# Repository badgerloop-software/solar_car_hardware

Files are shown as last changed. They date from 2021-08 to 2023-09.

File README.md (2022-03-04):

# solar_car_hardware
Repository for solar car electrical hardware made in Altium Designer. This project is set up to provide all documentation, design and data validation required for the Badgerloop Solar Car PCBs. This repository builds off of our previous work in the SpaceX Hyperloop Competition.

## Prerequisites
Altium only works on Windows. See  [Altium System Requirements](https://www.altium.com/documentation/18.0/display/ADES/Altium+Designer+-+((System+Requirements))") for more information. An internet connection is required to connect to the license server and dual monitors are nice to have. Microsoft Excel is required for BOM generation.

## Installation
1. Make an [Altium live account](https://live.altium.com/signin?prmGotoUrl=https://www.altium.com/altium-designer/) so you may work on Badgerloop's 10 person floating license
2. Contact Lucas Maddox or Shelby Riggleman to be added to the [Badgerloop Team Account](https://dashboard.live.altium.com/) and the Badgerloop [Github](https://github.com/badgerloop-software"). You may continue to step to step 8 without requiring an active license. If there is a delay for some reason, you can work on Altium training and practice on CAE computers or through [Citrix](https://remote.engr.wisc.edu/vpn/index.html), but we are usually able to add new users within 24 hours. Badgerloop currently supports Altium 21.2.0. 
3. Download the latest version of [Altium Designer](https://www.altium.com/products/downloads) 
4. Install Altium. Default file paths will work.
5. Install [Git Bash](https://gitforwindows.org/) Git Bash (or whatever BASH emulation tool you are comfortable with)
6. Open Git Bash
7. Type the following commands into the command prompt window:
   + cd ../..
   + mkdir git
   + cd git
   + git clone https://github.com/badgerloop-software/solar_car_hardware.git
   + cd hardware
   + git checkout -b <your-username_training>
   + Open Altium and sign in. You are now on a training branch that you will complete your first getting started project on if you are new to Altium. 
8. Go to User (Silhouette in the top right corner) -> License Management. Then Click Sign In and enter your username and password associated with Altium Live and accept the warning. It's also a good idea to check Sign me in when I start Altium Designer if you'd like to save a little time.

_NOTE: If you go click "Sign In" directly from User, you will be asked for a server address. This is not what you want. Go back to step 7 and hit License Management instead of Sign In._ 

8. Click Use to claim a license. If you are not using a valid license, you will be able to view files in Altium Designer but you will not be able to make edits. Ensure that you are choosing an Altium Designer License and not our PDN License. That's something else. 
9. You are now ready to use Altium. See [Training](#training) for more details on how to get started. 

## Github Basics
+ [Here](https://wiki.badgerloop.org/index.php/Github_How_To) is a breakdown of what git/github is and how Badgerloop utilizes it. If you'd like more information or a different description, [here](https://www.freecodecamp.org/news/learn-the-basics-of-git-in-under-10-minutes-da548267cc91/) is a pretty good page that breaks down the basics.

## Training 
+ Multivibrator Project: The Multivibrator Project from Altium is hands down the best training resource for getting started with Altium. We suggest that everyone new to PCB design complete this tutorial on their own prior to working on Badgerloop schematics or boards. While we want to help everyone as much as possible, it's on you to get a bit of a background. Feel free to ask Ezra, Shelby or Ryan if you have any issues with the tutorial. [Multivibrator Tutorial] (https://www.altium.com/documentation/altium-designer/from-idea-to-manufacture-driving-a-pcb-design-through-altium-designer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). This guide goes "From Idea to Manufacture" and drives a design all the way though rough-drawing your circuit, making library symbols and footprints, schematic capture, placement, layout, and routing, as well as manufacturing outputs. 
+ Additionally, keep an eye out for any Badgerloop sponsored training sessions! 

## Acknowledgements
+ [Altium](www.altium.com), for being an amazing sponsor! 
+ Dave Jones of the EEVBlog, as we'd have no idea what we were doing without his videos.

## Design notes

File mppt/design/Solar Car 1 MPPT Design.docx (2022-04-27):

Solar Car 1 MPPT Design

Starting Helpful links:

- Solar cell equivalent circuit: https://www.allaboutcircuits.com/technical-articles/circuit-designer-guide-to-photovoltaic-cells-solar-powered-devices/
- Boost converter MPPT simulation: https://www.youtube.com/watch?v=o9BOrAHH5E4
- Discussion on MPPT vs charge controlling: https://electronics.stackexchange.com/questions/519900/understanding-working-of-mppt-charger
- MPPT Charge Controller Reference Design for 12-V, 24-V and 48-V Solar Panels: https://www.ti.com/lit/ug/tiduej8a/tiduej8a.pdf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

Preliminary Questions:

Buck or boost converter?

- Contingent on motor voltage: if > 100V or so, want boost, if less consider buck
  - The reason for this is we want to be able to use integrated buck converter IC’s on the board for peripheral voltages (i.e. 12V, 3.3V) and these packages rarely are rated for VIN > 80V or so.

How does altering duty cycle of these converters move you along the solar IV curve?

- Buck:
  - Increasing duty cycle approaches short circuit (I increases)
  - Decreasing duty cycle approaches open circuit (I decreases)
- Boost:
  - Increasing duty cycle approaches short circuit (I increases)
  - Decreasing duty cycle approaches open circuit (I decreases)

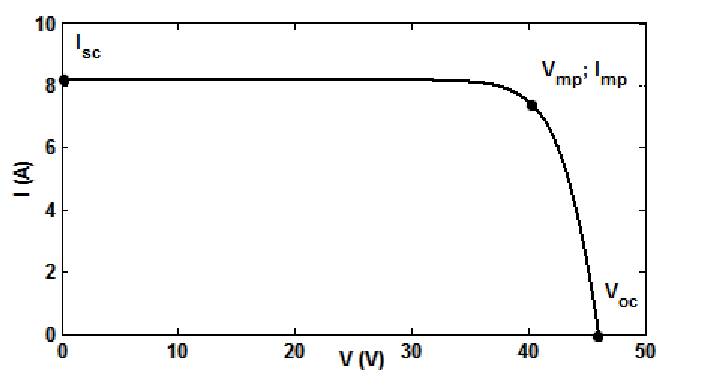
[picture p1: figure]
I-V curve of a solar panel. The three characteristic points (short... | Download Scientific Diagram

Decreasing duty cycle

Pictured: Relationship between duty cycle and position on IV curve. Applies to both buck/boost.

Can MPPT buck/boost converter be the same as the charge controller or do we need two with a DC link (large capacitor between the two)?

- In order to ideally use one controller as both, three things must be true/designed for:
  1. Can accurately do pure current control (NOT MPPT) when battery is charging
    - Must be able to distinguish Iload from Icharge
    - Develop charge algorithm to take over MPPT when Iload < Iarray
      - Two scenarios:
        - Iarray – Iload < ideal charge current for current SOC
          - Continue MPPT
        - Iarray – Iload > ideal charge current for current SOC
          - Current control necessary
      - To get charging current to decrease, the converter will have to increase the impedance of the converter by altering duty cycle (decrease on buck converter, decrease on boost converter) to utilize the decaying nature of current as voltage increases on the IV curve)
        - Must size pack to have max voltage to the voltage to where the minimum desired charging current lies on IV curve (or just max solar array voltage, as voltage is pretty constant at end of the IV curve).

Pictured: Increasing array voltage will decrease input current in a charging scenario.

  2. MPP on the solar array side remains unaffected regardless of what the battery voltage is. If the solar array is automatically “brought down” to the battery voltage, MPPT will be moot and we will just have a charger. Due to the rectifying diode or FET with dead-time on a boost converter, the output of the converter should always be >= battery voltage, and the solar array voltage will not be dictated by the battery.
  3. We design a hardware (NOT SOFTWARE) failsafe shutoff of converter if battery voltage is above certain threshold is implemented
    - Consider a comparator comparing battery voltage to reference voltage that turns off control FET
      - Needs to take into account battery voltage drop under load so battery doesn’t charge when at full SOC, but voltage appears lower because discharging : VBat = VBatNominal – (Iout*PackInternalResistance).
      - Potentially set this cutoff threshold to not charge above VBat = VBatNominal – IMaxExpected*PackInternalResistance.

What happens if the maximum power point impedance/duty cycle yields a different output voltage than the battery voltage? If operating at maximum power point, is the output power fundamentally “capped” by the ideal voltage source that is the battery?

This is a question because typically with buck and boost converters with a voltage source Vin, Vout = Vin *(D) and Vout = Vin( 1/(1-D)) respectively. (D = duty cycle). At first thought, one might think that if the MPP yields an output voltage at the inductor that is greater than the battery voltage, there is some loss in the difference between the inductor output and the battery when the inductor voltage is “brought down” after passing through the rectifying diode to the battery voltage.

Pictured: Ideal buck and boost output voltage transfer functions with voltage src Vin

The answer to this question is best answered by reviewing the fundamentals of inductors. Inductors will do whatever it takes to keep the current flowing in it from changing – creating a voltage across the inductor as necessary to do so. Given this, the inductor will only output as high of a voltage as necessary to keep the current that was flowing in the inductor “charge” state into the battery. There is no “excess voltage” that is being lost due to a duty cycle that would yield a higher voltage if a resistive load was connected.

Simulation:

In order to answer some of the above questions and get a better understanding of the operation of an MPPT boost converter, a characteristic simulation will be made of a solar array & converter that can be modified to fit desired array parameters.

Links referenced:

- https://www.youtube.com/watch?v=MZ-3HDjwPWw
- https://electronics.stackexchange.com/questions/257253/modeling-a-solar-panel-for-simulations
- http://www.intusoft.com/nlhtm/nl78.htm#The_Solar_Cell_SPICE_Model

Parameters for modeling custom solar array:

Voc = open circuit array voltage

Isc = short circuit array current

I0 = saturation current (of single cell). Hard to derive – informs open circuit voltage. Solar cell saturation current on the order of magnitude of 1e-10. Best derived from test data.

Derived parameters for modeling custom solar array:

N = emission coefficient

XTI = exponent temperature coefficient

IS = saturation current

EG = energy gap

To put these in the equivalent circuit for a solar cell, add a generic diode in the proper location as D1 below:

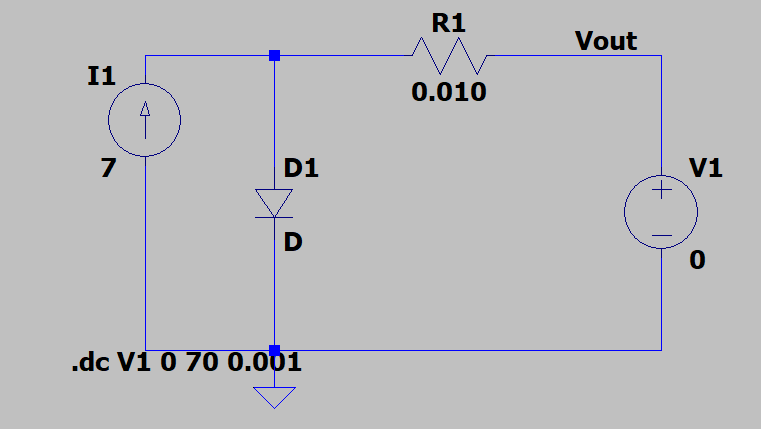
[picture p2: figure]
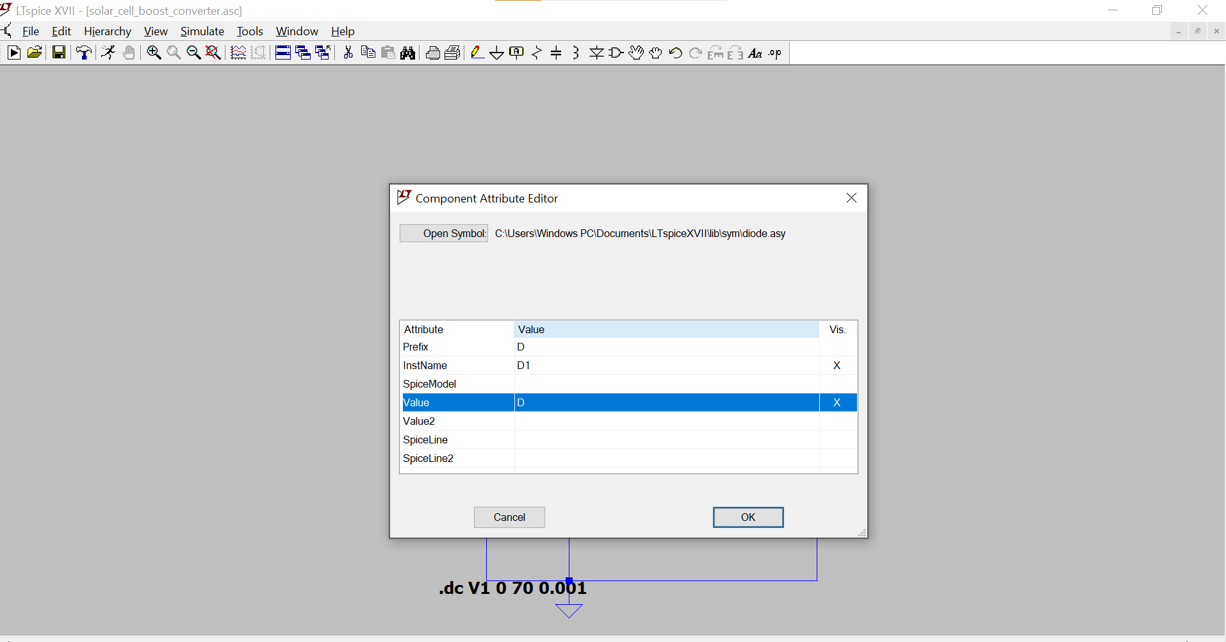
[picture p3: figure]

CTRL + Right click on the diode to bring up this menu:

Change the “value” Parameter to the custom name you’d like to call the diode – “DiodeSolarCell here:

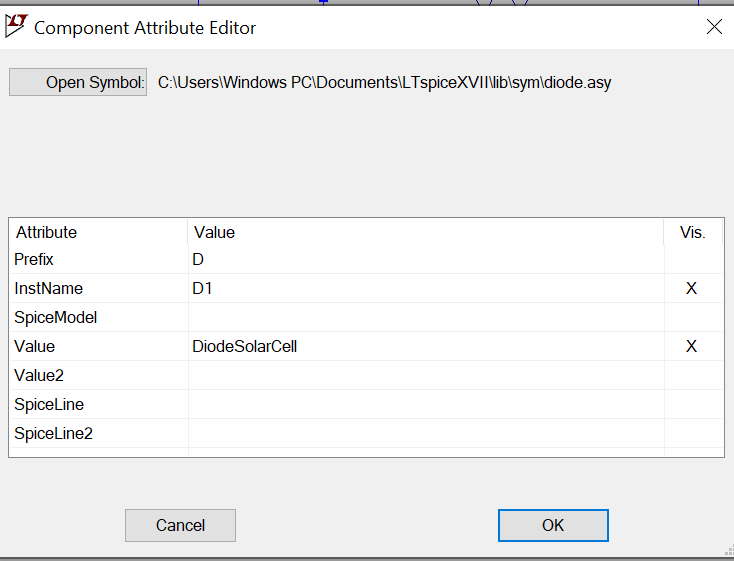
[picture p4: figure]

Add a spice directive with the following form to attribute calculated parameters to this diode:

.model <name_you_gave_diode> D LEVEL=1 IS=<calculated IS> N=<calculated_N> EG=<calculated_EG> XTI=calculated_XTI

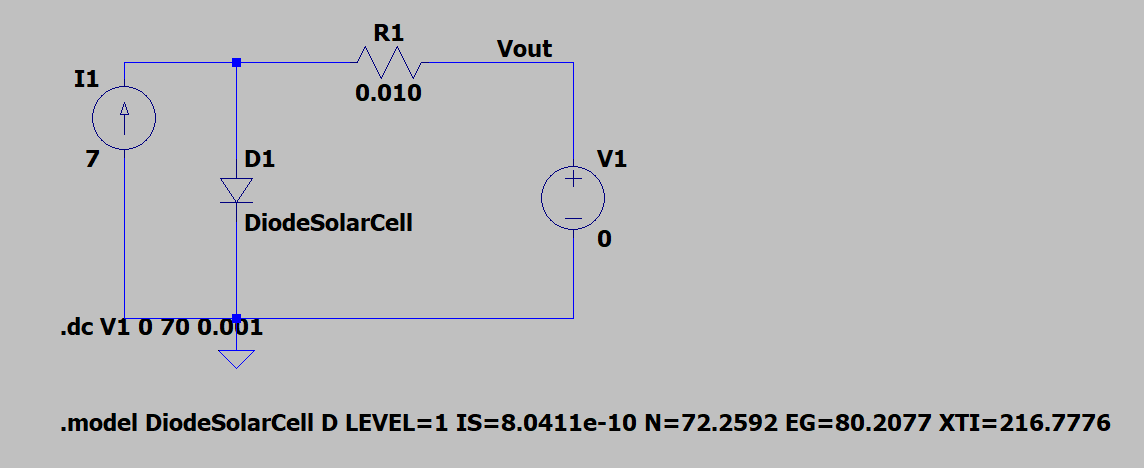
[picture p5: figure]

Example:

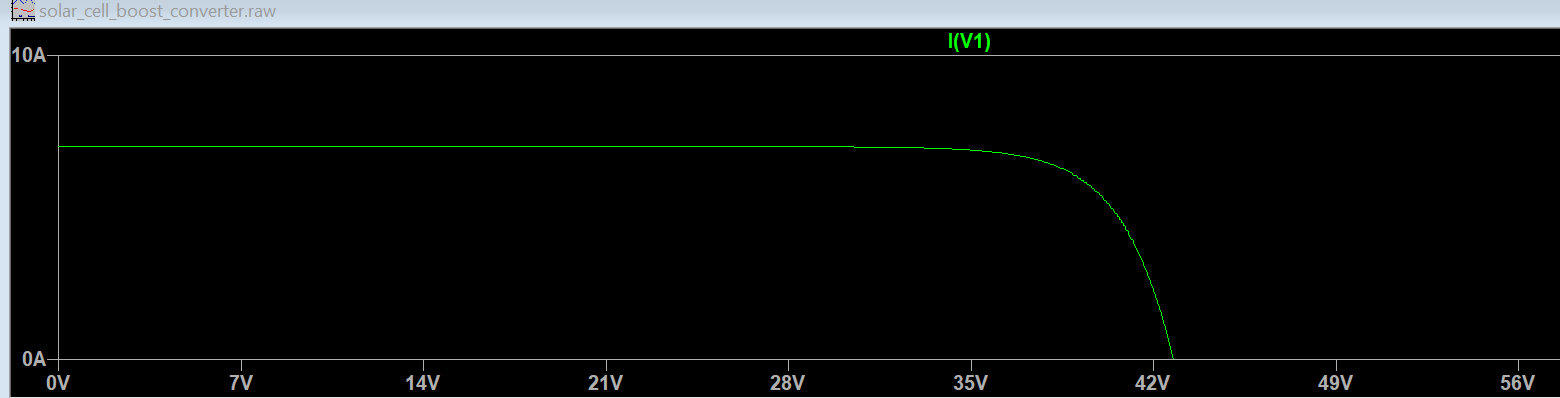
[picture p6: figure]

This should result in an I=V curve with the following shape when a dc sweep is ran on the model:

Boost converter simulation:

Hooking up the solar array model to a boost converter topology as shown below is helpful to understand the working principles and waveforms on various nodes of the MPPT. The actual “Maximum Power-point Tracking” would be a function of the output current of this model (to the battery and load). The dependent variable is the duty cycle of the MOSFET gate drive signal, simulated by V1 here.

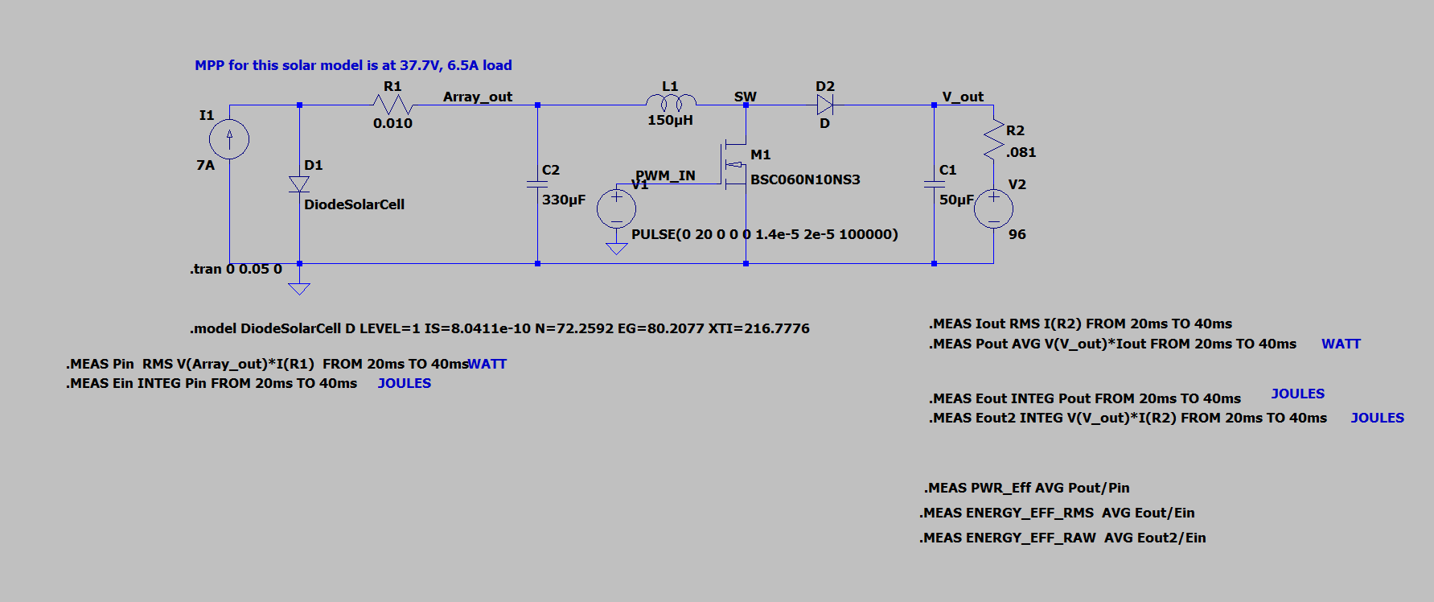
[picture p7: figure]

Solar array and battery specs

The solar array and battery specs are listed below. The solar array will have 3 individual strings that will be put in parallel to output to the battery pack. The decision for 3 individual strings was made to accommodate initial off the shelf MPPT solutions (found in next section), which have a maximum current rating of 7A, and allows for adequate marigin to boost from the solar array voltage to battery pack voltage (boost ratio > 1.1). In addition, multiple strings allow for individual maximum power-point tracking of each unique string in the event of varying iridescences between the strings (i.e. the back half of the car is in the shade).

- Pack nominal voltage: 96V
- Pack max voltage: 107V
- Number solar strings: 3
- Solar array string open circuit voltage: 57.12V
- Solar array string voltage: 48.72
- Solar array open circuit current per string: 6.34A
- Solar array mpp current per string: 6A
- Solar array mpp power = 876.96W

Solution Space

Elmar Race MPPT

This off the shelf option would allow for a quick, readymade solution for Solar Car 1. It is a boost converter with a minimum boost ratio of 1.1, max output voltage of 165V, and max output current of 7A. The peak conversion efficiency tops out at 99.6%. Perhaps more relevantly, At the maximum power point of our array (48.72V), the Elmar MPPT device shows an efficiency of 98.25%. Given the configuration of our solar array, we would need 1 Elmar MPPT per string, for a total of 3. At the cheapest unit cost of $2588.27, this would put the final BOM exceeding $8000, and proves prohibitively expensive among all of the other costs of building a solar car for the first time.

Custom In House Design

A custom design offers many advantages to an off the shelf solution with an additional assumption of risk. Foremost, a custom design can achieve a BOM of < $800, an order of magnitude more lucrative than the off the shelf solution. In addition to the immense learning opportunity it presents, it also provides more flexibility in the competition and bring-up environment. In the event of a malfunction of the device or user mistakes, a replacement part can be ordered for what is likely under $10, instead of bearing the lead time and cost of an entirely new off the shelf MPPT.

The risks include the additional time of design and testing, along with the novelty of power electronics to Badgerloop as an organization. There could easily be an oversight of a power electronics “gotcha” that requires the spinning of a board and delayed time until the solution is complete. With that being said, most of facets of building a solar car for the first time involve a degree of risk, and a custom MPPT approximates the degree of these risks.

Given the extremely constrained timeline that exists to build a first car within a year, building a converter that matches an off the shelf solution’s performance (namely efficiency) exactly will not be the sole determinant of a successful design, while still being the primary directive of the design. With an in house design, improving upon it can be an iterative process and provide learning opportunities to teams of the future for years to come. In order to minimize identified risks, the custom design can approximate the known interface of the Elmar MPPT (12V, GND, CAN) to allow for a swap with an Elmar MPPT in the event the car’s MPPT is the critical path in having a working car.

Path & Goals

With the advantages that a custom in-house design provides, and in the ambitious spirit of Badgerloop, an in-house design will be pursued with the following directives:

1) Consolidate these 3 MPPT devices into one sleeker, cheaper, simpler solution.
2) Achieve an efficiency of 97% or greater in design & ideal test conditions.
3) Learn about and implement fundamentals of power conversion and control in the context of a large embedded system.

Custom MPPT Design

Helpful links:

- Multiphase (&single phase) boost converter design: https://www.ti.com/seclit/wp/slup323/slup323.pdf
- MOSFET Losses in Switching Power supplies: https://fscdn.rohm.com/en/products/databook/applinote/ic/power/switching_regulator/power_loss_appli-e.pdf
- Boost converter design & power losses: https://www.powerelectronicsnews.com/the-dc-dc-boost-converter-part-2-power-supply-design-tutorial-section-5-2/
- System Design considerations for battery operated system: https://www.ti.com/download/trng/docs/seminar/Topic%206%20-%20DC-DC%20Power%20Conversion%20and%20System%20Design%20Considerations%20for%20Battery%20Operated%20System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

Note: The TI single phase reference paper was heavily cited in development of this design. Additionally, the calculations performed for many of these design decisions were performed and saved in an excel sheet “Converter_calculations.xlsx” saved in the mppt/design directory that cite the source for the pertinent equation.

Design Outline:

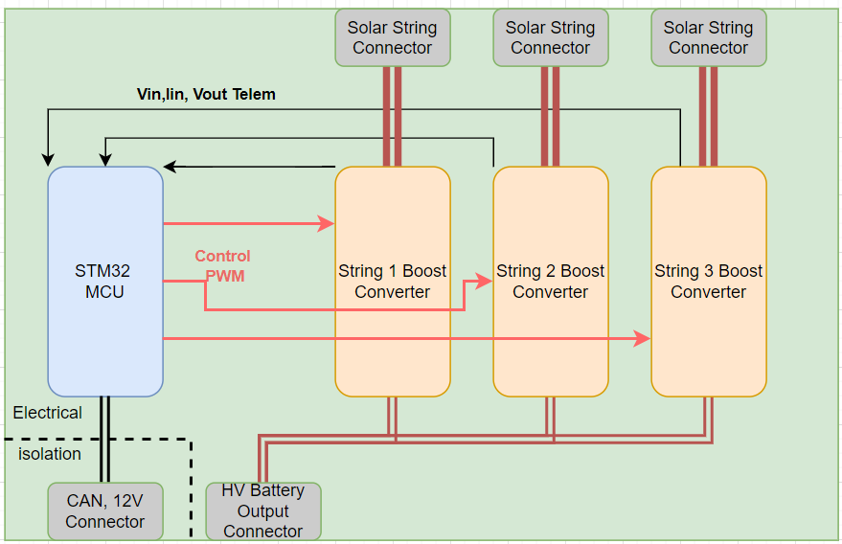
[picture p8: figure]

MPPT Block Diagram

There are three boost converters, one for each solar string. Each converter is capable of operating at the highest solar string values, as well as their maximum power point, for the maximum output power of the solar array of 876W. Each converter is uniquely controlled to its maximum power point by a Nucleo STM32 microcontroller based on telemetry from solar string voltage, solar string current, and battery (output) voltage. The three converters are tied together at the output for the battery. The operating mode for output (battery charging vs MPPT), along with desired on-board telemetry is communicated via a galvanically isolated CAN interface that connects to the rest of the low voltage electrical system.

Final Design:

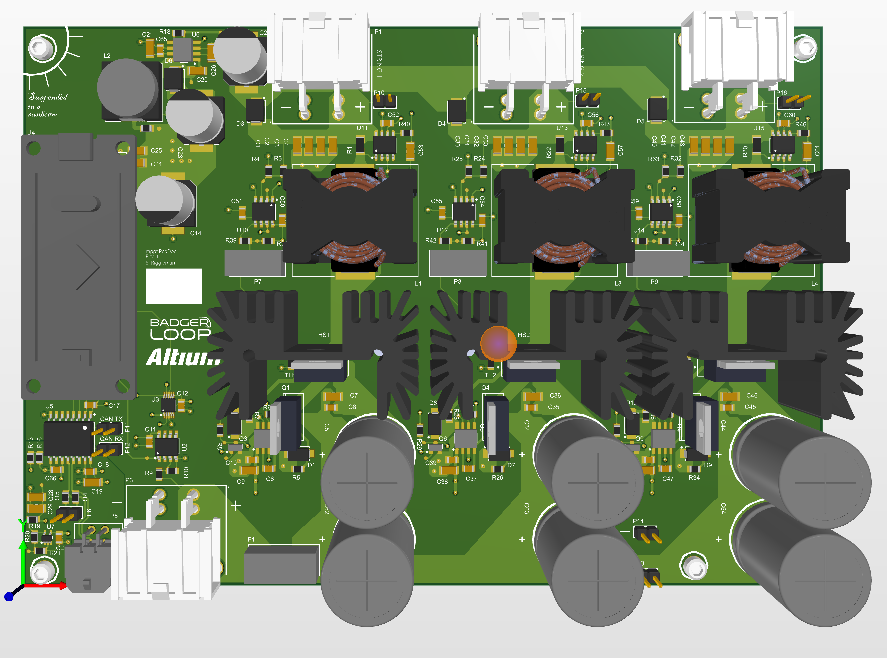
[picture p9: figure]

Final MPPT PCB layout, Rev1

At the completion of this initial design, we are able to predict that the solution will be able to perform at 97.05% efficiency, while being 1/10 the cost of an off the shelf solution, while simultaneously having a smaller form factor (7” x 4.9”) than a necessary grouping of off the shelf solutions.

Boost converter design:

Consideration: Multiphase boost converter

Initially, a multiphase (2 phase) boost converter was considered as a solution for the main power converter. There are some advantages to this path, as per TI “When considering higher output currents, a multiphase boost converter provides many advantages over a single-phase option for higher power boost converters. Advantages are seen in efficiency, thermal performance and size”. With this option, the 3 strings would be fed into a singular dual phase converter, with one output to the battery. There would be 1 power point being “tracked”. After doing initial calculations on this solution, it proved more favorable to transition to a multi string single phase design. The primary reason was too high of switching losses at switching frequency needed to keep the inductor in CCM. Using higher inductance values could allow moving to a smaller frequency (which is what we do on new design) and decrease switching losses, but parts with necessary inductance values with a > 9A saturation current are few, and we want options in supply shortage. In addition, having unique MPPT's per string allows for most efficient MPPT tracking and prevention of false MPPT peaks when combining multiple strings together if one is shaded.

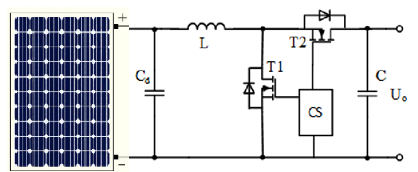
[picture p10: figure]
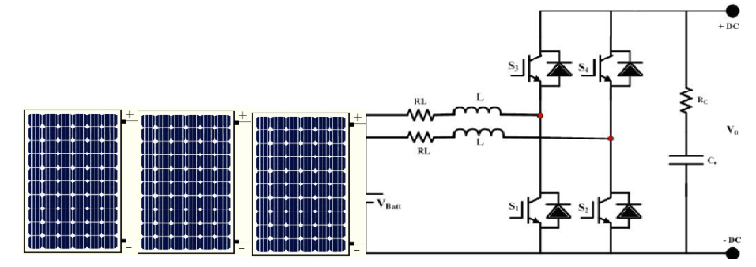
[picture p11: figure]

Multiphase configuration Single phase, 3 string configuration

Single Phase Converter Design:

The boost converter circuits operate as all boost converters do. The low side FET (boost FET) is turned on for a fraction of the switching frequency (proportional to the control duty cycle), during which current starts to increase through the inductor and store energy in its magnetic field. When the boost FET is turned off, the inductor creates a voltage across it equal to Vout – Vin to keep current flowing through the inductor. Current through the inductor decreases through this duration, but flows to the output through the high side FET or rectifier diode, whichever is populated.

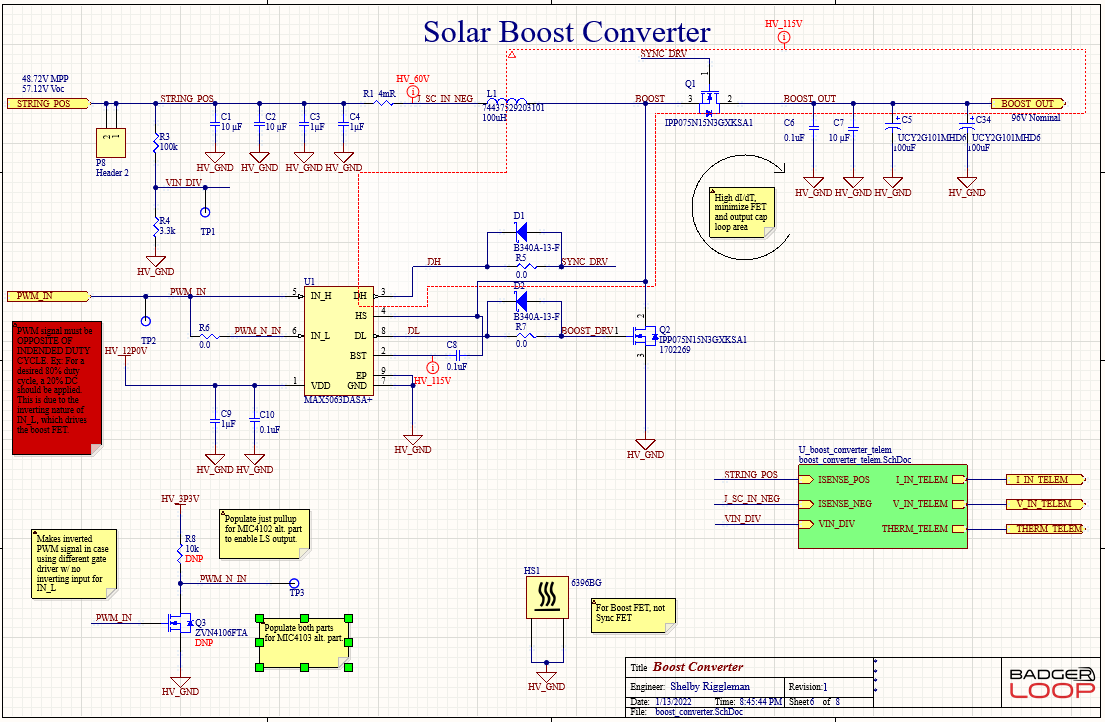
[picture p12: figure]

Instance of MPPT Boost Converter

Operating Frequency:

One of the key variables that dictates converter efficiency is the frequency that the transistors switch (switching frequency). The lower the frequency, the lower the transitional, QRR, QOSS, and inductor AC/Core losses are. Typical switching converter frequencies range from 100kHz to 2MHz. For this converter, a low frequency of 80kHz will be pursued. The consequence of operating at a lower frequency is that a larger inductor needs to be used, since more energy must be stored due to a longer off period where the inductor must be the source of current. This frequency is the same as the PWM signal applied to the gate driver. As frequency decreases, PWM resolution from the STM 32 increases as well. At 80kHz, the PWM signal should have 9 bit or .19% duty cycle step resolution.

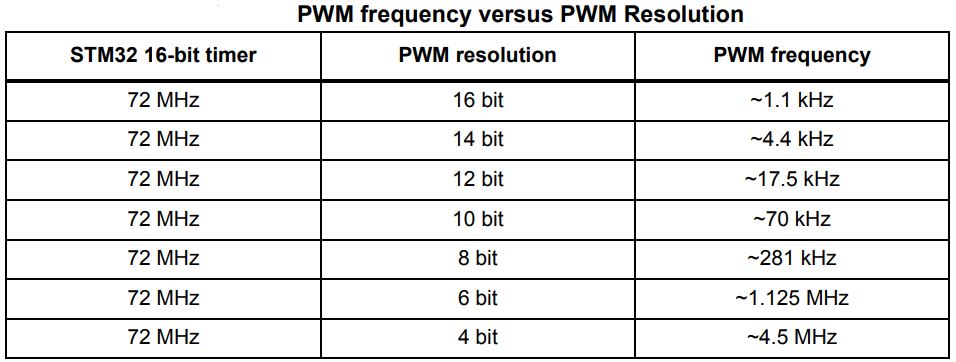
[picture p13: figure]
STM32 PWM Example - Timer PWM Mode Tutorial – DeepBlue

STM32 PWM resolution vs frequency

Inductor:

The inductor is chosen to keep it in continuous conduction mode at the operating frequency, while having a saturation current rating exceeding the expected average current. The inductor chosen was 74437529203101 by Wurth-Elektronic to satisfy these requirements. It is 100uH and has a 9.4A saturation current with a DCR of 22.9mOhm. This inductance value results in a 2.99A ripple current (50% of DC MPP of 6A).

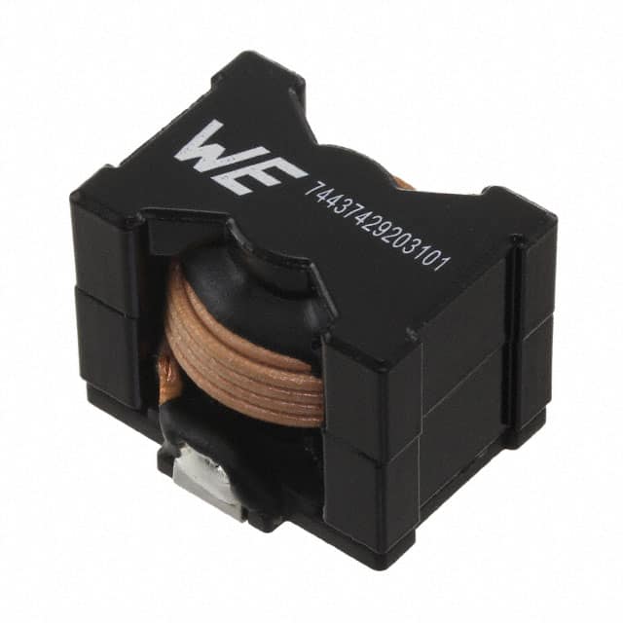
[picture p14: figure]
74437529203101 Würth Elektronik | Inductors, Coils, Chokes | DigiKey

74437529203101

FET:

The MOSFET is chosen by being within the voltage (100V) and current (7A) spec, along with having low RDSON and low switching charge. The former results in low DC rms losses, while low switching charge allows for quick transition times for minimal loss during the miller plateau.

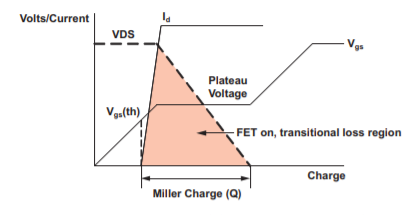
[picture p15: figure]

Transitional region loss in MOSFET (Vth to end of miller plateau)

Additionally, low Qrr (reverse recovery charge) and Qoss (output charge) assist in having low switching losses. Per calculations in the TI boost converter document, QRR is the primary source of losses in this converter, totally 3.6W loss per string.

QRR loss equation

A TO-220 package FET was chosen for this design due to ease of thermal dissipation (many heatsinks are available for this package), along with compatibility with many other FETs in the event the part is no longer available, whereas D2PAK packages are somewhat more customized.

The part chosen was IPP075N15N3 G, with a RDSON of 7.2mOhm, switching charge of 70nC, QOSS of 179nC, and a Qrr of 478nC.

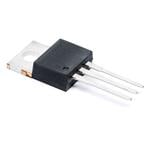
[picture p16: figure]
Infineon Technologies IPP075N15N3 G

IPP075N15N3 G

FET Driver:

The primary characteristic looked for in a FET driver was availability and max sink/source current. The max sink/source current is what drives the FETs on and off, so that they can have snappy on and off transitions for low switching losses. A driver with sink source of 2A or greater was pursued for this purpose. Another essential characteristic is that the driver must be able to drive the output voltage + Vgs on the high side FET. For our application this is 100V + 12V = 112V. The FET driver should have a HS voltage output rating in excess of this number.

The gate driver must also have dead-time built in, so that the two transistors are never on at the same time and a shoot through from the battery to ground occurs.

Additionally, a gate driver with an inverting input of the PWM signal is desired, as the two transistors need to be on opposite of one another, and because the PWM signal is the driving signal to drive the boost FET, there must be an inverted copy of it to turn the sync FET on or off in the opposite manner of the boost FET.

The MAX5063DASA+ was the primary part selected for the gate driver. It features built in dead time, an inverting PWM input, and a source/sink drive current of 2A, with a maximum HS gate drive of 125V.

To combat the part shortage, there are 3 alternative parts that share the same footprint as the original that can be substituted in the event that the MAX5063DASA+ is not available. The MAX15019BASA+ is a drop in replacement with a higher sink/source, but was unavailable during initial design. The MIC4102 is a replacement with an inverting input for the LS driver. However, an extra resistor must be populated (noted in schematic sheet) to enable the LS driver. The MIC4103YM is another replacement part with a compatible footprint, but an inverting FET and pullup resistor must be populated (also in the schematic sheet), as there is no internal inversion of the PWM signal.

IMPORTANT NOTE:

Because these gate drivers are used most frequently for buck converters, the high side FET is the “control” FET (i.e. the PWM signal drives the high side FET with a certain duty cycle and is directly related to the desired output voltage). With our boost converter, the low side FET is the control FET, and typical conceptions of how a duty cycle effects the output voltage is with respect to the boost FET. Because of this, the main PWM signal applied to the gate driver from firmware must be the opposite of what is intended to be. For example, if one wants an 80% duty cycle on the boost FET, the PWM signal must be 20%, so that when the signal is inverted to the low side driver, it is 80%, and the HS driver is at 20% duty cycle.

Thermal:

The hottest component on the board, and the one necessitating thermal management is the boost FET. The boost FET incurs full transitional losses, QRR losses, and QOSS losses. In our design, the boost FET will be dissipating 5.34W. With a junction-ambient thermal impedance of 62K/W, this would put the device over its 175C rating.

With a target max junction temperature of 125C and an expected maximum ambient temperature 45C, the permissible junction-ambient temperature difference is 80C. Hence, the largest possible thermal impedance that a heatsink can possess is 14.96 K/W. With a derating of 33% to account for the point-load nature of the transistor connection (heat is not evenly applied to the heatsink), we get a maximum thermal impedance from junction to ambient of 9.33 K/W.

With a thermal interface material (TIM) interface between the FET and heatsink, assuming a thermal conductivity of 0.79 W/MC, and an area of application of 0.000112 square meters, and a thickness of .04mm, the thermal resistance between the FET case and the heatsink is 0.45W/K.

In addition, the junction-case thermal impedance is 0.5K/W.

With a 9.33 -0.45 – 0.5 = 8.38K/W desired heatsink thermal impedance, the 6396BG was chosen. It has a natural convection (no airflow) thermal impedance of 5.6K/W.

This results in a maximum expected junction temperature of 89.9C.

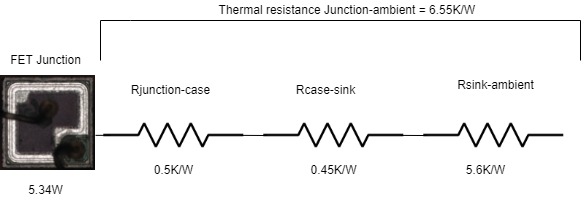
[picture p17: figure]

Thermal impedances of boost FET with heatsink

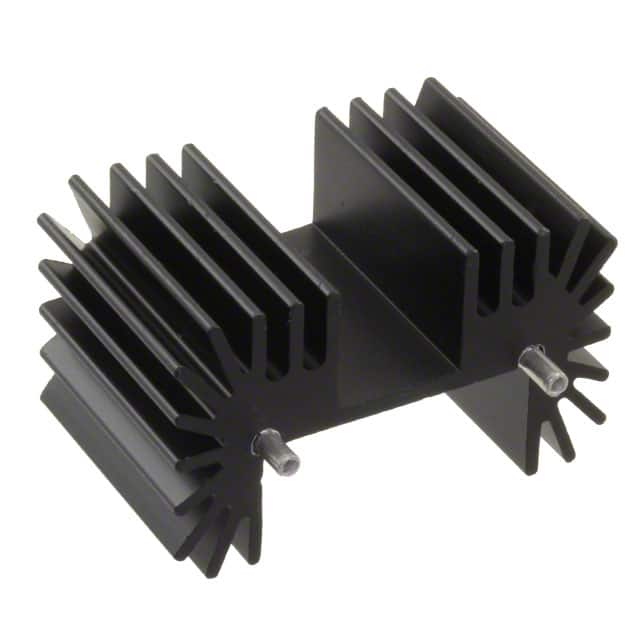
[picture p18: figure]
6396BG

6396BG Heatsink

Output Capacitor:

The output capacitor directly affects the voltage ripple on the output, and must also be rated for the full ripple current of the boost converter, as unlike a buck converter, the output sees the a full change from maximal current into the capacitor to full current output from the capacitor.

With each string converter having 200uF of capacitance on the output, the max voltage ripple will be 0.115V. There will be two 100uF electrolytic capacitors in parallel with a 1.75A RMS ripple current rating each to absorb and supply the bulk of the expected 2.84 Arms ripple current. In addition, .1uF and 10uF ceramic capacitors will be used to absorb and supply the fast edges of the current due to its lower inductance.

The UCY2G101MHD6 100uF capacitor was selected for the main output capacitor(s).

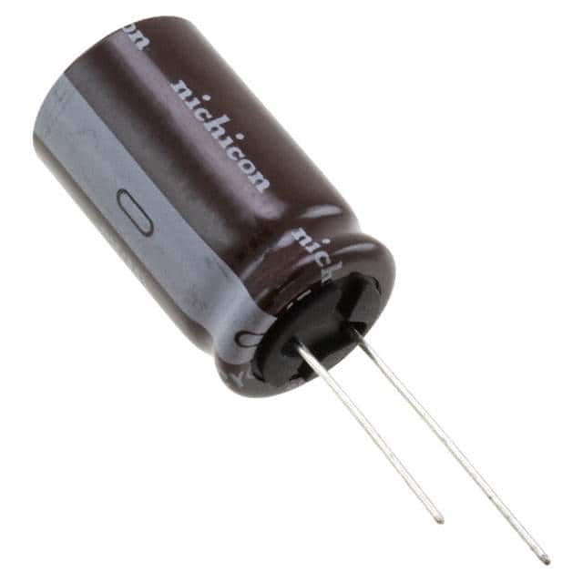
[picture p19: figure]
UCY Series 33mm

UCY2G101MHD6

Efficiency:

With the summation of inductor DCR losses, inductor AC/core losses, FET conduction, QOSS, Qrr, transitional losses, MCU losses, and driver losses, there are approximately 26.32 watts being lost as heat on this board. At maximum power-point of 876W, that equates to a 97% efficiency for the converter.

It is important to note that this is this is the efficiency for the entire MPPT system (control included). Having the entire MPPT system on one board allows us to be on the same tier of efficiency as multiple (perhaps off the shelf) MPPTs of higher efficiency. For example, if we were to use three 99% efficient off the shelf MPPTs (one for each string), the total efficiency would be 0.99*0.99*0.99 = 97% efficiency.

Tabulated Losses
Source | Per String (if applicable) (W) | Total (W)
Inductor DCR Losses: | 0.841567272 | 2.524701816
Core/Winding Losses: | 0.0178 | 0.0534
Boost FET Conduction Loss: | 0.127656 | 0.382968
SyncFET Conduction Loss: | 0.131544 | 0.394632
Boost FET Transitional Loss: | 0.86016 | 2.58048
Qoss Losses | 1.37472 | 4.12416
Qrr losses | 3.67104 | 11.01312
FET Driver | 0.370272 | 1.110816
MCU | | 3.6
Isense Resistors | 0.18 | 0.54
Total | | 26.32427782
Efficiency @ MPP | | 0.969982351

Losses and Efficiency

Open Questions:

There are a few open questions regarding the boost converter design as follows that are not design prohibitive, but would be good to seek answers to in continued development of this device

1) How does one assess stability of the closed loop system (gain/phase margin)?
2) What are the advantages and disadvantages of operating in continuous conduction mode vs discontinuous conduction mode?

Telemetry & Control

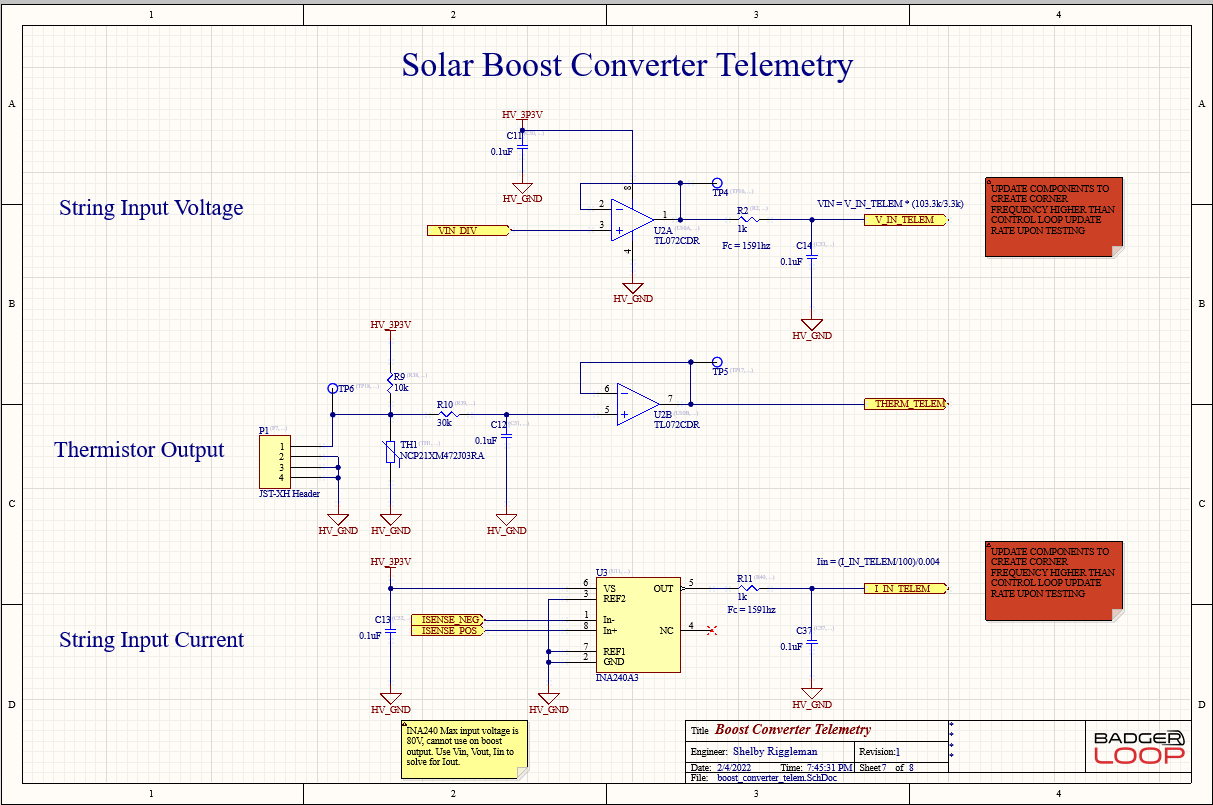
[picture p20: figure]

Boost Converter Telemetry Circuits

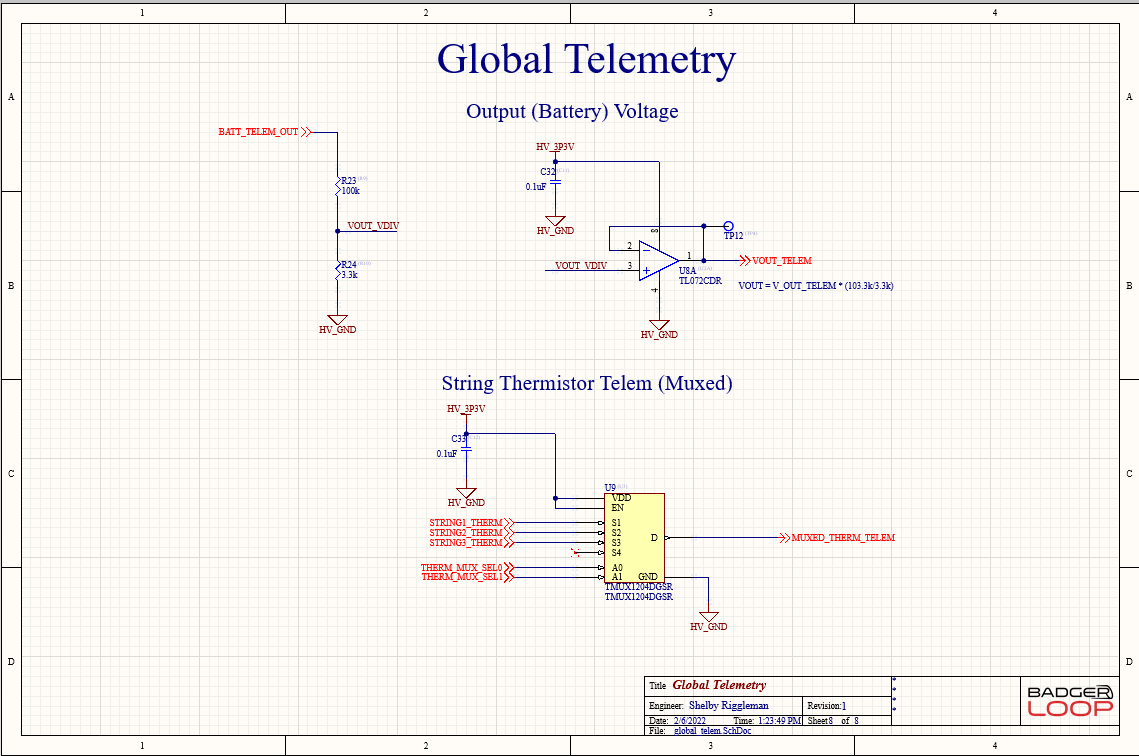
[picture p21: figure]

Global Telemetry Circuits

Feedback for control to the MCU is facilitated by current sense resistors on the input of the boost converter, and a unique voltage divided output for the string input voltage. There is one global voltage divider for the output voltage that is connected to the battery. Each string output current can be derived from Pin = Pout * efficiency. One thermistor attached to the boost FET of each converter has its voltage selected to be read by the MCU through a discrete analog MUX. This is not a critical part of operating telemetry, so it may be cycled through and read at a low rate such as 2hz. Telemetry from the boost circuits are fed through op amps so that if there was an over-voltage event the op amps would saturate instead of the MCU being fried. There is an output low pass filter on these op-amps to filter out switching frequencies and record the dc operating points. These filters must have a cutoff frequency higher than the loop update rate of the MCU control code, so that changes can be promptly read and responded to in the control loop.

MCU & CAN Interface

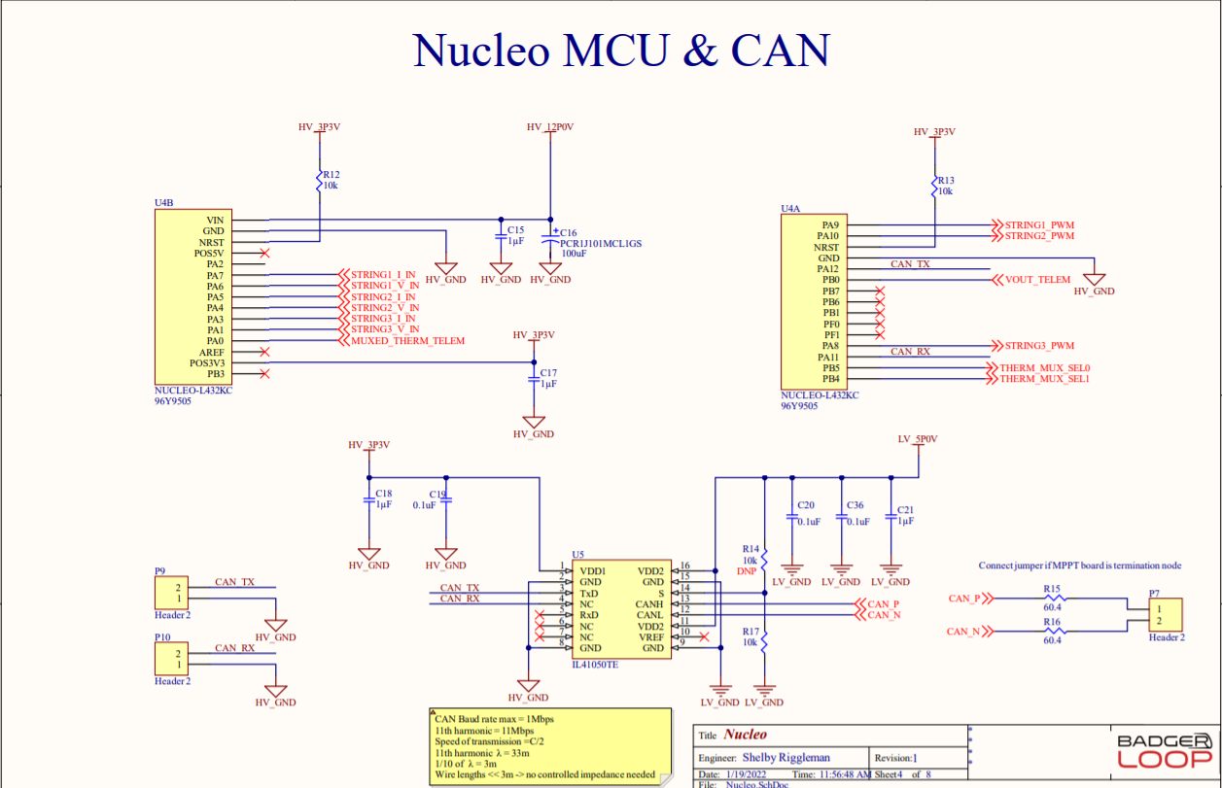
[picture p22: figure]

MCU Selection

The Nucleo STM-32 platform was selected to perform the primary control & telemetry functions on the MPPT board. Badgerloop has familiarity (and importantly stock) with the Nucleo-L432KC platform. It is equipped with 10 Successive Approximation Register ADC channels with 12bit, 5MSPS functionality. The Nucleo-L432KC is also able to output multiple PWM channels that will control the boost converters at 80khz with 9 bits of resolution.

Firmware

Helpful Links:

- Practical Guide to implementing MPPT algorithms: https://ww1.microchip.com/downloads/en/appnotes/00001521a.pdf

Platform:

The firmware will be ran on an STM32 microcontroller (Either STM32L432KC or STM32F303K8T6) located on a Nucleo breakout board that is fitted onto the PCB.

Requirements:

The firmware must be able to:

  - Receive CAN messages (Nucleo TX on pin PA12, RX on PA11) from the LV Beaglebone indicating:
    - MPPT mode or battery charge mode
    - Maximum charge current (when in charge mode)
  - Perform a periodic health indicator (may be a CAN message checksum/ message received indicator) that will open the battery contactor if not received after period of time
  - Read ADCs on pins PA7, PA5, and PA3 and derive the String input current based on the voltage on these pins
  - Read ADCs on pins PA6, PA4, and PA1 and derive the String input voltage based on the voltage on these pins
  - Read ADC on pin PB0 to derive the battery voltage based on the voltage from this pin
  - Deliver a ~80,000hz PWM signal on pins PA9, PA10, and PA8.
  - Perform MPPT tracking using a perturb and observe algorithm implementing a PID control scheme that modifies the PWM duty cycle to deliver desired output current to the battery (maximum possible in MPPT mode, prescribed current in battery charge mode).
    - String input current, string input voltage, and pack voltage is derived from ADC input values
    - Converter output currents per string (Iout) is solved for using Pin = Pout: Iin*Vin =Vout *Iout.
    - Battery input current is a summation of calculated converter output currents.
    - NOTE: PWM signal must be OPPOSITE OF INDENDED DUTY CYCLE. Ex: For a desired 80% duty cycle, a 20% DC should be applied. This is due to the inverting nature of IN_L, which drives the boost FET.

Nice to haves:

  - Telemetry back on the CANbus to the Beaglebone indicating measured values (string input voltage, input current, output current)
  - Temperature monitoring from thermistors on pin PA0.
    - There is one thermistor per boost converter string (3 total), and these three signals are muxed through a discrete device, whose output is selected by Nucleo GPIO pins PB4 & PB5.

Testing

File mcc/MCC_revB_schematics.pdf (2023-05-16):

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
Badgerloop Electrical
133 Engineering Research Building 1500 Engineering Drive
Madison, Wi 53706
2

## TEMPLATE PCB COVER

4/6/2023 | 9:19:32 PM
cover.SchDoc

Title

Engineer:
Date:
File:

Revision:
Time: | Sheet | of

# BOARD TEMPLATE

# SOLAR CAR 2021

# REV 1

# DO NOT EDIT

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
## Power

S. Riggleman, M. Farah | *
4/6/2023 | 9:19:33 PM
Power.SchDoc

Title

Engineer:
Date:
File:

Revision:
Time: | Sheet | of
V-POS12V | LV 12V -> 5V | V-POS5V

R25
0.0
FB/NC 1
GND 2

NC 3

IN 4
OUT 5

U4

ST715CR

R28
10k

TP1

TP2

C5
0.1uF

C6

### 10 µF

R27
1k

R26
30k

Added two resistors here for 31k for BOM consolidation

100V

1uF

C4

GND | GND

GND

GND GND

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
## Nucleo & Serial

M. Farah, S. Riggleman | *
4/6/2023 | 9:19:33 PM
Nucleo.SchDoc

Title

Engineer:
Date:
File:

Revision:
Time: | Sheet | of

VIN
GND
NRST
POS5V
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
AREF
POS3V3
PB3

96Y9505

U1B

NUCLEO-L432KC

PB4

PB5

PA11

PA8

PF1

PF0

PB1

PB6

PB7

PB0

PA12

GND

NRST

PA10

PA9

96Y9505

U1A

NUCLEO-L432KC

V-POS12V

Crz_modeA
Crz_modeB
Crz_set
Crz_rst

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
V-POS3.3V

CAN_TX

CAN_RX

GND

GND

R9
10k

V-POS3.3V

R11 10k

Speed_Sig

GND
GND

V-POS3.3V LED+

R20
10k

ZVN4106FTA

FET1

Brk_Status

R29
10k

GND

ZVN4106FTA

FET2

R10
2k

R17
1.2k

2

3

1 4 8 TL072CDR

U6A
TL072CDR

2

3

1 4 8 TL072CDR

U3A
TL072CDR

6

5

7

TL072CDR

U3B

TL072CDR

MC_Acc_Pot_5V

GND

Brk_In

Acc_Out

R24 10k

GND GND

R31 10k

V-POS5V

GND

20k

R18

R23 20k
R30 20k

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
Acc_In

Brk_Out

MC_Brk

MCU_Rev_Sel

Acc_Sig Brk_Sig

Main_Telem

Eco_Telem

FR_Out

MC_Status

Speed_MCU

R22
10k

Brk_2_Status

P_Brk_Status

FR_Telem

2

3

1 4 8 TL072CDR

U5A
TL072CDR

MC_Brk_Pot_5V

GND

FR_Telem

R21
10k

R19
10k

V-POS12V

# Inputs

# Outputs

MC_Acc

Need to change to single
channel op amps

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
## Connectors

McGregor Farah | *
4/6/2023 | 9:19:33 PM
Connectors.SchDoc

Title

Engineer:
Date:
File:

Revision:
Time: | Sheet | of

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
43045-2000

# Motor Controller Interface

GND

GND

1

2

P1

43045-0200 | 1

2

P9

43045-0200 | 1
| 2

P10

43045-0200

Eco_Switch+

1
2
3
4

P6

43045-0400

V-POS5V

GND

Acc_Sig

1
2
3
4

P8

43045-0400

V-POS5V

GND

Brk_Sig

1
2

P2

43045-0200

1
2
3
4

P5

43045-0400

1
2
3
4

P7

43045-0400

WM1814-ND

1
2
3
4

P3

43045-0400

V-POS12V

GND

CAN_H
CAN_L

Crz_modeA
Crz_modeB

Crz_set
Crz_rst

GND

Brk_Status

GND

1
2

P13

Header 2

1
2

P14

Header 2

V-POS5V

V-POS12V

1
2

P12

Header 2

V-POS3.3V

GND

1
2

P11

Header 2

CAN_H
CAN_L

# Debug Headers

# Driver Inputs

# Main IO

GND

Main_Switch+

GND

Main_Telem

GND

100k

R4

200k

R6

Eco_Telem

GND

MC_12VOUT | FR_Telem MC_Eco

V-POS3.3V

300k

R3

100k

R5

MC_Acc_Pot_5V

MC_Brk

MC_Acc

MC_Eco | Eco_Switch+

MC_LED+

FR_Out

MC_Speed_Sig

MC_Brk_Pot_5V

MCU_12VOUT | Main_Switch+

1
2

P16

43045-0200

Brk_2_Status

GND

1
2

P17

43045-0200

P_Brk_Status

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
* | *
4/6/2023 | 9:19:34 PM
CAN.SchDoc

Title

Engineer:
Date:
File:

Revision:
Time: | Sheet | of
V-POS3.3V | V-POS5V

C1
0.1uF | C2
0.1uF

VDD1 1
GND1 2
RXD 3
NC 4
NC 5
TXD 6
GND1 7
GND1 8 | GND2 | 9
GND2 | 10 NC | 11 CANL | 12 CANH | 13 NC | 14 GND2 | 15 VDD2 | 16

U2

ISO1050DWR

CAN_RX

CAN_TX

GND
GND
GND | GND

CAN_H
CAN_L

1
2

P15

Header 2

R2
60.4

R1
60.4

Connect jumper if MCC board is termination node

CAN_H

CAN_L

CAN Baud rate max = 1Mbps
11th harmonic = 11Mbps
Speed of transmission #NAME?
11th harmonic λ = 33m
1/10 of λ = 3m
Wire lengths << 3m -> no controlled impedance needed

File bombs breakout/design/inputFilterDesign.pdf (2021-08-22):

## Input filter design for switching power supply:

Written by Michele Sclocchi michele.sclocchi@nsc.com
Application Engineer
National Semiconductor

Basic step-down simple switcher power supply:

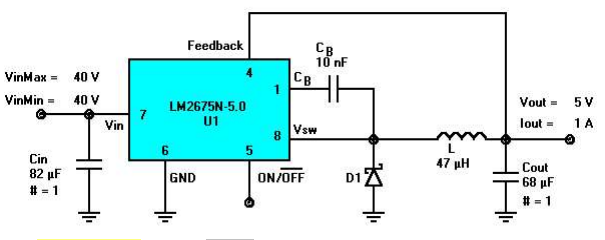
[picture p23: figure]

Input parameters | Results
-Maximum input voltage: | Vinput | 35V :=
-Output current: | Iout | 10 A :=
-Output voltage: | Vout | 5V :=

-Output inductor:

inductance: | Lo | 33 := μH
DC resistance: | RL := 0.088Ω
-Output capacitor: | Co | 68 := μF
ESR | 0.09 := | Ω
-Duty cycle: | D | 0.458 :=
-Output impedance: | Ro

Vout
Iout
:= | Ro 0.5 A- 2

kg s- 3
m

2
= | | |
i | 1 2000 := .. | f
i

100

( ) i 200 -
500
:=

w
i
| f i

rad
s
:= | s i

2πj w
i

:=

1

-Input impedance of the power supply:

Zii

Ro R + L

D

2

### 1 si

Lo
Ro R + L

ESR

Ro R L
Ro R + L

+

+ | Co
+ | s( )i
2
LoCo

Ro ESR +
Ro R + L
+ |

### 1 si

+ ( | ) Ro ESR + | Co
:= |

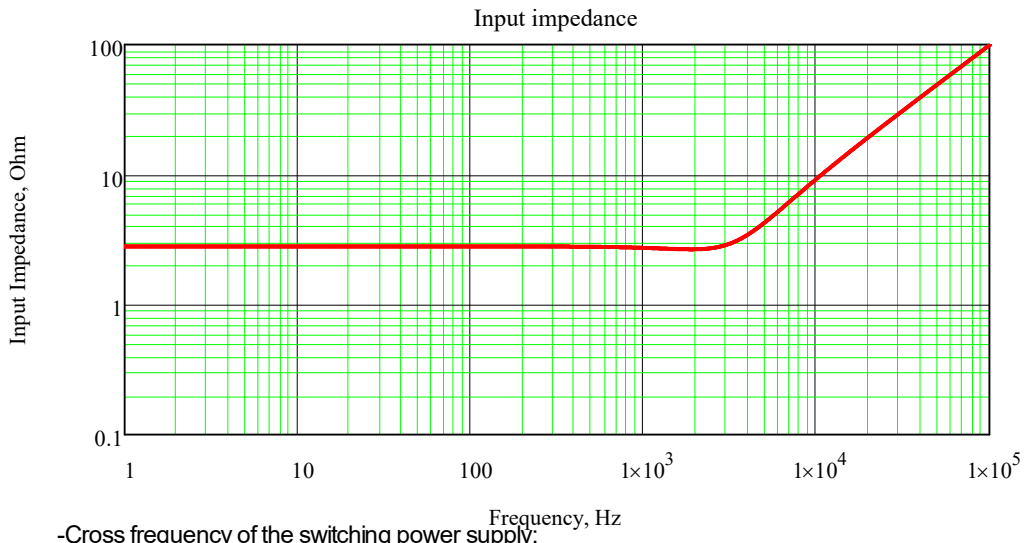
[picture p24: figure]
Input impedance; Frequency, Hz Input Impedance, Ohm

-Cross frequency of the switching power supply:

Fcross 32kHz :=

To meet the noise filtering requirements the input filter has to have the corner frequency around one decade below the bandwidth of the feed back loop of the power supply.

-Cut of frequency of the input filter: | fc | 5kHz :=
-Cut off frequency in radiant: | ωc | fc 2 := π ωc 3.142 104
- s
- 1
= |
-Maximum input impedance of the power supply: | Rin | 25 ohm :=
-Input Capacitance of the power supply: | C := 15μF

2

### - UNDUMPED LC FILTER:


-Inductance calculated:

L

1

ωc

2C

:= | L 67.547 = | μH

-Damping factor:

ζ

L
2 Rin | L C
:= | ζ = 0.042

-Inductor used:
Lf | 1 := μH
Rf | 0.030 := | Ω

-Capacitor used:

Cf | 33 := μF
ESRci | 0.150 := | Ω

-Cut off frequency of the filter:

fcfilter1

1
2π Lf Cf
:= | fcfilter1 = 27.705 kHz

-Transfer function:

Z1i

Rf si

:= + Lf

Z2i

ESRci 1
s
i

Cf

:= +

Z2eqi

Z2i

Rin

Z2i

+ Rin

:=

Filteri

### 20 log

Z2eqi

Z2eqi

Z1i

+

:=

3

Transfer function; Zfi; Input impedance

Frequency, Hz Gain, Db

-Filter output impedance:

Frequency, Hz Input Impedance, Ohm

Filter output impedance
Power supply input impedance

In order to avoid oscillations it is important to keep the peak output impedance of the filter below
the input impedance of the converter.
The two curves should not overlap.

### -PARALLEL DAMPED FILTER:

In most of the cases a parallel damped filter meet easily the damping and impedance requirements.


The purpose of Rd is to reduce the output peak impedance of the filter at the cutoff frequency. The capacitor Cd blocks the DC component of the input voltage.

-Damping resistance:

Rd | Lf Cf
:= | Rd 0.174 A- 2

kg s- 3
m

2
= | | |
Cd | 4 Cf := | Cd 132 = | μF
ESRcd | 0.200 := | Ω

Z3i

1
s
i

Cd

:= + ESRcd + Rd

Z3eq2i

Z2eqi

Z3i

Z2eqi

Z3i

+

:=

-Transfer function:

Filter2i

### 20 log

Z3eq2i

Z3eq2i

Z1i

+

:=

5

Transfer function; Output impedance

Frequency, Hz Gain, Db

Undumped Filter
Parallel damped filter

-Filter output impedance:

Frequency, Hz Output Impedance, Ohm

Undumped filter
Power supply input impedance

-SERIES DAMPED FILTER:

sr


1
2π Lf Cf

:=

-Series inductor: | n3

2
15

:=

Ld | Lf n3
:= | | Ld 0.133 = | μH

-Series damping resistance:

Rds Lf
Cf
:= | Rds 0.174 A- 2

kg s- 3
m

2
= | | |

Z3si

Rds si

:= + Ld

Z13i

Z1i

Z3si

Z1i

Z3si

+

:=

-Transfer function:

Filter3i

### 20 log

Z2i

Z2i

Z13i

+

:=

7

Transfer function; Output impedance

Frequency, Hz Gain, Db

Undumped Filter
Series damped filter
Parallel damped filter

With the series damped filter the attenuation at high frequency is attenuated.

-Filter output impedance:

Frequency, Hz Output Impedance, Ohm

Undumped filter
Power supply input impedance

-MULTIPLE FILTER SECTIONS:


-First LC filter:

L1

Lf
4
:= | L1 0.25 = | μH | RL1 | 0.1 := | Ω

C1

Cf
4
:= | C1 8.25 = | μF | ESRc1 | 0.120 := | Ω
fm1 | 1
2π L1 C1
:= | fm1 110.821 kHz = |

-Second LC filter:
L2 | 7 L1 := | L2 1.75 = | μH | RL2 | 0.1 := | Ω
C2 | 4 C1 := | C2 33 = μF | ESRc2 | 0.120 := | Ω
fm2 | 1
2π L2 C2
:= | fm2 20.943 kHz = |
Rd4 | L1 C2
:= | Rd4 0.087 A- 2

kg s- 3
m

2
= | | |
Ld4 | L1
8

:=

Zm1i

s
i
:= L1 + RL1 | Zm2i

1
s
i

C1

:= + ESRc1

Zm3i

Rd4 si

+ Ld4 ( | ) s
i
L2 + RL2 ( | )

Rd4 si

+ Ld4 ( | ) s
i

+ L2 + RL2

:= | Zm4i

1
s
i

C2

:= + ESRc2

-Transfer function:

9

Filter4i; 20 log; Transfer function

Frequency, Hz Gain, Db

Two stage filter
Series damped filter
Parallel damped filter

-Filter output impedance:

Output impedance

Frequency, Hz Output Impedance, Ohm

Two stage filter
Series damped filter
Power supply input impedance

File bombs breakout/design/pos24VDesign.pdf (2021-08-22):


Printed : 09/14/2019 | Copyright © 2014 Analog Devices Inc.

## Designer : Castle

## Project Date : 9/14/2019

## Project Name : LTC3114-1 24V Supply

## Output Rails : Vout1 = 24.09V / 0.5A (max.)

## Vin : 18V (min.), 24V (nom.), 30V (max.)

# LTC3114-1 Supply Design Summary Report

## Output Rails : Vout1 = 24.09V / 0.5A (max.)

## Vin : 18V (min.), 24V (nom.), 30V (max.)

## LTC3114-1 Solution - Simplified Schematic


## Rail # 1 : Vin = 24V, Vout1 = 24.09V

## LTC3114-1 Solution - Efficiency & Loss Estimations


### * Estimations For CCM Mode Only. Inductor AC Losses Entered by User

### * Estimations For CCM Mode Only. Estimations Based On Small Signal Avg. Model

## Rail # 1 : Vin = 24V, Vout1 = 24.09V, Iout1 = 0.5A

## LTC3114-1 Solution - Loop Gain & Load Transient Estimations


## LTC3114-1 Solution - Summary


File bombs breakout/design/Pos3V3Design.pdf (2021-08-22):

TPS5420 3.3V Supply Design

Design Parameters
Vin_min≔8 V | Vin_ripple≔300 mV
Vin_max≔35 V | Vout_ripple≔50 mV
Vout_nom≔3.3 V | Iout_max≔2 A
K_ind≔0.2 | Fsw≔500 kHz | Fsw fixed by TPS5420

Input Capacitors

C_bulk≔10 ⋅ 10⁻⁶ F | ESRmax≔0.002086 Ω | ESL_max≔1200 ⋅ 10⁻⁹ H
Vin_ripple_calc≔Iout_max⋅―――――+ | =
| 0.25
| C_bulk⋅Fsw

((Iout_max⋅ESRmax)) 0.104 V

I_cin≔――――=

Iout_max
2
1 A | Choose input capacitors rated for at
least 50V with a ripple current capacity for each at 3A at 500kHz

Output Filter Components

Inductor Selection

L_min≔Vout_nom⋅―――――――――――――=

| ((Vin_max-Vout_nom))
((Vin_max)) ⋅K_ind⋅ Iout_max⋅Fsw⋅ 0.8
| | ⎛⎝1.868 ⋅ 10⁻⁵⎞ ⎠ H

L_nom≔18 ⋅ 10⁻⁶ H

I_L_rms≔ | | =

⎛
⎜
⎝

Iout_max⋅ Iout_max+―1

| 12 ⎛ ⎜
⎝――――――――――――

((Vout_nom⋅ ((Vin_max-Vout_nom)))) ((Vin_max⋅L_nom⋅Fsw⋅ 0.8))

⎞
⎟
⎠

2 ⎞
⎟
⎠

0.5
2.001 A
I_L_peak≔ | =

⎛
⎜
⎝
| Iout_max+―Vout_nom ―――⋅ ――――――――

((Vin_max-Vout_nom))
1.6 ⋅Vin_max⋅L_nom⋅Fsw

⎞
⎟
⎠

2.113 A

| Choose an inductor with at least 2.5A rms and 3A

saturation current

Output Capacitor Selection

Created with PTC Mathcad Express. See www.mathcad.com for more information.

Fco≔10 kHz Target Crossover frequency

Cout≔――――――――――=

1
((3357 ⋅L_nom⋅Fco ⋅Vout_nom))

⎛⎝2.735 ⋅ 10⁻⁴⎞

⎠ ―s ―⋅ ―

### 6 A

3
kg ⋅

### 2 m

4
~100uF

Nc≔5 Select 5x 22uF capacitors to approximate 100uF

Cout_esr_max≔――――――=

1
((2 ⋅π⋅Cout⋅Fco))

0.058 ―kg―⋅ ―

### 2 m

4
s ⋅

### 5 A

3
~88mOhms

Vpp_max≔Cout_esr_max⋅Vout_nom⋅――――――――――=

((Vin_max-Vout_nom))
Nc ⋅Vin_max⋅L_nom⋅Fsw⋅ 0.8

0.003 ―kg―⋅ ―

### 2 m

4
s ⋅

### 5 A

2

6mV pk-pk ripple

Ensure output cap is rated for Vout + 1/2 ripple voltage + derating, ~ 5.006*1.3=6.5V, round up to 25V

Estimate ripple current max at 150mA

Output Voltage Set

R1≔10 kΩ | R1_min≔R1 ⋅.999 | R1_max≔R1 ⋅ 1.001

R2≔――――――――=

R1 ⋅ 1.221
((Vout_nom-1.221 V))
| ⎛⎝5.873 ⋅ 10³ ⎞

⎠ ―1
A
| | 5.75KOhms +/-0.1%
R2_min≔R2 ⋅.999 | R2_max≔R2 ⋅ 1.001
Vout_min≔R1_min⋅―――+ | =
| 1.221 R2_max 1.221 V 3.296 V
Vout_max≔R1_max⋅―――+ | =
| 1.221 R2_min 1.221 V 3.304 V

Boot Cap

Datasheet gives 0.01uF for the boot capacitor. NP0/COG preferred

Duty Cycle (Max)

D_max≔――――=

Vout_nom
Vin_min⋅η
η≔0.9 | D_min≔――――= | 0.458 Vout_nom
Vin_max⋅η

0.105

Catch Diode
D_reverse_voltage_min≔Vin_max+0.5 V =35.5 V

D_iout_max≔Iout_max+0.5 ⋅ I_L_rms=3.001 A
Diodes, Inc B340A has a reverse voltage of 40V, forward current of 3A and forward voltage drop of 0.5V
If≔Iout_max⋅ ((1- D_min))=1.79 A If_2≔Iout_max⋅ ((1- D_max))=1.083 A

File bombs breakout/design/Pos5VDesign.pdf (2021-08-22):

TPS5420 5V Supply Design

Design Parameters
Vin_min≔10 V | Vin_ripple≔300 mV
Vin_max≔35 V | Vout_ripple≔50 mV
Vout_nom≔5 V | Iout_max≔2 A
K_ind≔0.2 | Fsw≔500 kHz | Fsw fixed by TPS5420

Input Capacitors

C_bulk≔10 ⋅ 10⁻⁶ F | ESRmax≔0.002086 Ω | ESL_max≔1200 ⋅ 10⁻⁹ H
Vin_ripple_calc≔Iout_max⋅―――――+ | =
| 0.25
| C_bulk⋅Fsw

((Iout_max⋅ESRmax)) 0.104 V

I_cin≔――――=

Iout_max
2
1 A | Choose input capacitors rated for at
least 50V with a ripple current capacity for each at 3A at 500kHz

Output Filter Components

Inductor Selection

L_min≔Vout_nom⋅―――――――――――――=

| ((Vin_max-Vout_nom))
((Vin_max)) ⋅K_ind⋅ Iout_max⋅Fsw⋅ 0.8
| | ⎛⎝2.679 ⋅ 10⁻⁵⎞ ⎠ H

L_nom≔33 ⋅ 10⁻⁶ H

I_L_rms≔ | | =

⎛
⎜
⎝

Iout_max⋅ Iout_max+―1

| 12 ⎛ ⎜
⎝――――――――――――

((Vout_nom⋅ ((Vin_max-Vout_nom)))) ((Vin_max⋅L_nom⋅Fsw⋅ 0.8))

⎞
⎟
⎠

2 ⎞
⎟
⎠

0.5
2.002 A
I_L_peak≔ | =

⎛
⎜
⎝
| Iout_max+―Vout_nom ―――⋅ ――――――――

((Vin_max-Vout_nom))
1.6 ⋅Vin_max⋅L_nom⋅Fsw

⎞
⎟
⎠

2.162 A

| Choose an inductor with at least 2.5A rms and 3A

saturation current

Output Capacitor Selection

Created with PTC Mathcad Express. See www.mathcad.com for more information.

Fco≔10 kHz Target Crossover frequency

Cout≔――――――――――=

1
((3357 ⋅L_nom⋅Fco ⋅Vout_nom))

⎛⎝1.805 ⋅ 10⁻⁴⎞

⎠ ―s ―⋅ ―

### 6 A

3
kg ⋅

### 2 m

4
~100uF

Nc≔5 Select 5x 22uF capacitors to approximate 100uF

Cout_esr_max≔――――――=

1
((2 ⋅π⋅Cout⋅Fco))

0.088 ―kg―⋅ ―

### 2 m

4
s ⋅

### 5 A

3
~88mOhms

Vpp_max≔Cout_esr_max⋅Vout_nom⋅――――――――――=

((Vin_max-Vout_nom))
Nc ⋅Vin_max⋅L_nom⋅Fsw⋅ 0.8

0.006 ―kg―⋅ ―

### 2 m

4
s ⋅

### 5 A

2

6mV pk-pk ripple

Ensure output cap is rated for Vout + 1/2 ripple voltage + derating, ~ 5.006*1.3=6.5V, round up to 25V

Estimate ripple current max at 150mA

Output Voltage Set

R1≔10 kΩ | R1_min≔R1 ⋅.999 | R1_max≔R1 ⋅ 1.001

R2≔――――――――=

R1 ⋅ 1.221
((Vout_nom-1.221 V))
| ⎛⎝3.231 ⋅ 10³ ⎞

⎠ ―1
A
| | 3.24KOhms +/-0.1%
R2_min≔R2 ⋅.999 | R2_max≔R2 ⋅ 1.001
Vout_min≔R1_min⋅―――+ | =
| 1.221 R2_max 1.221 V 4.992 V
Vout_max≔R1_max⋅―――+ | =
| 1.221 R2_min 1.221 V 5.008 V

Boot Cap

Datasheet gives 0.01uF for the boot capacitor. NP0/COG preferred

Duty Cycle (Max)

η≔0.9 D_min≔――――= Vout_nom Vin_max⋅η
0.159 D_max≔――――=

Vout_nom
Vin_min⋅η

0.556

Catch Diode
D_reverse_voltage_min≔Vin_max+0.5 V =35.5 V

D_iout_max≔Iout_max+0.5 ⋅ I_L_rms=3.001 A
Diodes, Inc B340A has a reverse voltage of 40V, forward current of 3A and forward voltage drop of 0.5V
If≔Iout_max⋅ ((1- D_min))=1.683 A If_2≔Iout_max⋅ ((1- D_max))=0.889 A

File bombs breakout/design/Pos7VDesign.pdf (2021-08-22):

TPS5420 7V Supply Design

Design Parameters
Vin_min≔10 V | Vin_ripple≔300 mV
Vin_max≔35 V | Vout_ripple≔50 mV
Vout_nom≔7 V | Iout_max≔2 A
K_ind≔0.2 | Fsw≔500 kHz | Fsw fixed by TPS5420

Input Capacitors

C_bulk≔10 ⋅ 10⁻⁶ F | ESRmax≔0.002086 Ω | ESL_max≔1200 ⋅ 10⁻⁹ H
Vin_ripple_calc≔Iout_max⋅―――――+ | =
| 0.25
| C_bulk⋅Fsw

((Iout_max⋅ESRmax)) 0.104 V

I_cin≔――――=

Iout_max
2
1 A | Choose input capacitors rated for at
least 50V with a ripple current capacity for each at 3A at 500kHz

Output Filter Components

Inductor Selection

L_min≔Vout_nom⋅―――――――――――――=

| ((Vin_max-Vout_nom))
((Vin_max)) ⋅K_ind⋅ Iout_max⋅Fsw⋅ 0.8
| | ⎛⎝3.5 ⋅ 10⁻⁵⎞ ⎠ H

L_nom≔36 ⋅ 10⁻⁶ H

I_L_rms≔ | | =

⎛
⎜
⎝

Iout_max⋅ Iout_max+―1

| 12 ⎛ ⎜
⎝――――――――――――

((Vout_nom⋅ ((Vin_max-Vout_nom)))) ((Vin_max⋅L_nom⋅Fsw⋅ 0.8))

⎞
⎟
⎠

2 ⎞
⎟
⎠

0.5
2.003 A
I_L_peak≔ | =

⎛
⎜
⎝

Iout_max+―Vout_nom ―――⋅ ――――――――

| ((Vin_max-Vout_nom)) 1.6 ⋅Vin_max⋅L_nom⋅Fsw ⎞ ⎟ ⎠
2.194 A
| Choose an inductor with at least 2.5A rms and 3A saturation current

Output Capacitor Selection

Fco≔10 kHz Target Crossover frequency

Cout≔――――――――――=

| 1
((3357 ⋅L_nom⋅Fco ⋅Vout_nom))
| ⎛⎝1.182 ⋅ 10⁻⁴⎞ ⎠ ―s ―⋅ ― 6 A

3
| kg ⋅ 2 m

4

Created with PTC Mathcad Express. See www.mathcad.com for more information.

~100uF

Nc≔5 Select 5x 22uF capacitors to approximate 100uF

Cout_esr_max≔――――――=

1
((2 ⋅π⋅Cout⋅Fco))

0.135 ―kg―⋅ ―

### 2 m

4
s ⋅

### 5 A

3
~88mOhms

Vpp_max≔Cout_esr_max⋅Vout_nom⋅――――――――――=

((Vin_max-Vout_nom))
Nc ⋅Vin_max⋅L_nom⋅Fsw⋅ 0.8

0.01 ―kg―⋅ ―

### 2 m

4
s ⋅

### 5 A

2

6mV pk-pk ripple

Ensure output cap is rated for Vout + 1/2 ripple voltage + derating, ~ 5.006*1.3=6.5V, round up to 25V

Estimate ripple current max at 150mA

Output Voltage Set

R1≔10 kΩ | R1_min≔R1 ⋅.999 | R1_max≔R1 ⋅ 1.001

R2≔――――――――=

R1 ⋅ 1.221
((Vout_nom-1.221 V))
| ⎛⎝2.113 ⋅ 10³ ⎞

⎠ ―1
A
| | 1.8KOhms +/-0.1%
R2_min≔R2 ⋅.999 | R2_max≔R2 ⋅ 1.001
Vout_min≔R1_min⋅―――+ | =
| 1.221 R2_max 1.221 V 6.988 V
Vout_max≔R1_max⋅―――+ | =
| 1.221 R2_min 1.221 V 7.012 V

Boot Cap

Datasheet gives 0.01uF for the boot capacitor. NP0/COG preferred

Duty Cycle (Max)

η≔0.9 D_min≔――――= Vout_nom Vin_max⋅η
0.222 D_max≔――――=

Vout_nom
Vin_min⋅η

0.778

Catch Diode
D_reverse_voltage_min≔Vin_max+0.5 V =35.5 V

D_iout_max≔Iout_max+0.5 ⋅ I_L_rms=3.002 A
Diodes, Inc B340A has a reverse voltage of 40V, forward current of 3A and forward voltage drop of 0.5V
If≔Iout_max⋅ ((1- D_min))=1.556 A If_2≔Iout_max⋅ ((1- D_max))=0.444 A

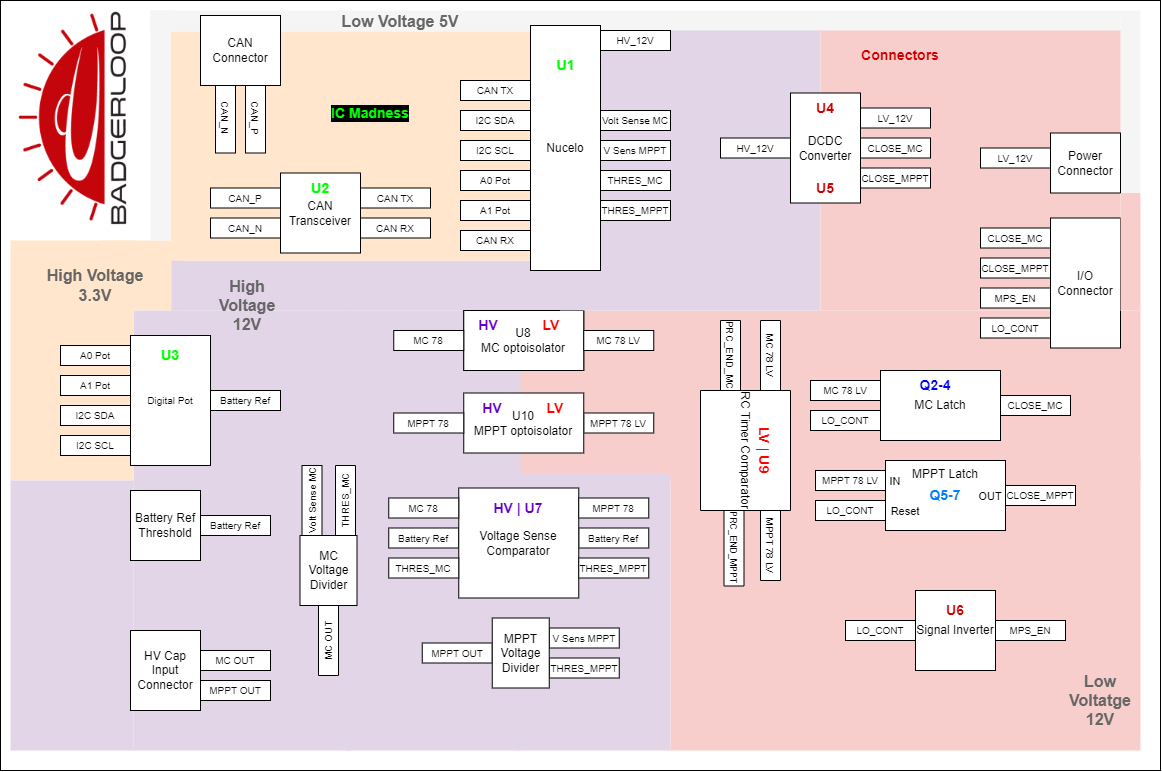
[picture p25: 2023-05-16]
hv_controller/design/HV Breakoutboard Layout Diagram.png

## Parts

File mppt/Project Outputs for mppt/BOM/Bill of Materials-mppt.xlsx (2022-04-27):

Comment | Description | Designator | Footprint | LibRef | Quantity
10 µF | 10 µF ±10% 100V Ceramic Capacitor X6S 1206 (3216 Metric) | C1, C2, C7, C16, C24, C28, C30, C31, C36, C40, C41, C46 | SMD-1206C | C3216X6S2A106K160AC | 12
C1206C105K1RACTU | Ceramic Capacitor, Multilayer, Ceramic, 100V, 10% +Tol, 10% -Tol, X7R, 15% TC, 1uF, Surface Mount, 1206 | C3, C4, C9, C11, C13, C15, C21, C25, C29, C32, C33, C38, C42, C43, C48, C70 | SMD-1206C | C1206C105K1RACTU | 16
UCY2G101MHD6 | Cap Aluminum Lytic 100uF 400V 20% (18 X 31.5mm) Radial 7.5mm 875mA 12000h 105C Automotive Bulk | C5, C34, C44, C62, C63, C64 | UCY2G101MHD6 | UCY2G101MHD6 | 6
0.1uF | Cap Ceramic 0.1uF 250V X7T 10% SMD 0805 125°C Blister Plastic T/R | C6, C8, C10, C12, C14, C17, C18, C19, C20, C26, C27, C35, C37, C39, C45, C47, C49, C51, C52, C53, C55, C56, C57, C59, C60, C61, C65, C67, C68, C69, C71, C72, C73, C74, C75, C76, C77, C78, C79, C80, C81, C82, C83, C84, C85, C86 | SMD-0805C | CGA4J3X7T2E104K125AA | 46
PCR1J101MCL1GS | CAP ALUM POLY 100UF 20% 63V SMD | C22, C23 | CAPAE110103X126M | PCR1J101MCL1GS | 2
B340A-13-F | DIODE SCHOTTKY 40V 3A SMA | D1, D2, D7, D8, D9, D10 | DIOM4326X20N | B340A-13-F | 6
S320 | Diode Schottky 200V 3A 2-Pin BGA MICROSTAR JUNIOR | D3, D4, D5, D6 | DIOM4436X26N | S320 | 4
TSP10H200S S1G | Rectifier Diode, Schottky, 1 Phase, 1 Element, 10A, 200V V(RRM), Silicon, TO-277A | D11, D12, D13 | TSP10H200S S1G | TSP10H200S S1G | 3
150V | Zener Diode, 150V V(Z), 6.12%, 1.25W, Silicon, Unidirectional, DO-214AC | D14 | CAPM3216X18N | BZG03C150-HM3-08 | 1
Diode General Purpose_2 | DIODE GEN PURP 20V 350MA SOD323 | D15, D16, D17, D18, D19, D20 | SODFL250X110-2N | Diode General Purpose_2 | 6
3568 | FUSE HOLDER MINI AUTO PC | F1 | Fuse Holder 30A 500V 1 Circuit Blade Through Hole | 3568 | 1
6396BG | TO-220/218 Packages 5.60 C/W Thermal Resistance Extruded Heat Sink | HS1, HS2, HS3 | 6396BG | 6396BG | 3
74437529203101 | Inductor, 100Uh, 11.2A, 20%, Shielded Rohs Compliant: Yes | L1, L3, L4 | 7443752903101 | 74437529203101 | 3
SRR1260A-561K | Ind Power Shielded Wirewound 560uH 10% 1KHz 22Q-Factor Ferrite 880mA T/R | L2 | SRR1260A-561K | SRR1260A-561K | 1
7443251000 | General Purpose Inductor, 10uH, 20%, 1 Element, SMD, 4040 | L5, L6, L7 | INDP105102X50N | 7443251000 | 3
LED RED 0603 | Red 631nm LED Indication - Discrete 2V 0603 (1608 Metric) | LED1 | LED 0603 RED | LED RED 0603 | 1
4-40 Mount Hole |  | MH1, MH2, MH3, MH4 | MH | 4-40 Mount Hole | 4
0431605302 | Conn Power HDR 2 POS 7.49mm Solder RA Thru-Hole 4 Terminal 1 Port Sabre™ Tray | P1, P2, P3, P4 | CONN HDR 2POS 7.50MM | 0431605302 | 4
43045-0400 | Male connector dual row 90° 3 mm Pole no. 2x2 Micro-Fit, 43045-0400, Molex | P5 | 430450400 | 43045-0400 | 1
Header 2 | Header, 2-Pin | P6, P10, P11, P12, P13, P14 | Pin Header 1x2 TH Pitch 2.54mm | Header 2 | 6
JST-XH Header | JST-XH CONN HEADER VERT 4POS 2.5MM | P7, P8, P9 | JST - XH 4 Pos | JST-XH Header | 3
IPP075N15N3GXKSA1 | Single N-Channel 150 V 7.5 mOhm 70 nC OptiMOS Power Mosfet - TO-220-3 | Q1, Q2, Q4, Q5, Q7, Q8, Q10 | IPP075N15N3 G | IPP075N15N3GXKSA1 | 7
MMBT3906-7-F | Small Signal Bipolar Transistor, 0.5A I(C), 45V V(BR)CEO, 1-Element, PNP, Silicon, TO-236AB | Q3 | SOTFL103P240X110-3N | MMBT3906-7-F | 1
MMBT100 | Small Signal Bipolar Transistor, 0.5A I(C), 45V V(BR)CEO, 1-Element, NPN, Silicon | Q6, Q9, Q11, Q12 | SOTFL103P240X110-3N | MMBT100 | 4
0.01 | Fixed Resistor, Metal Strip, 2W, 0.01ohm, 1% +/-Tol, 100ppm/Cel, Surface Mount, 2512 | R1, R22, R30 | SMD-2512 | PMR100HZPFU10L0 | 3
1k | RES SMD 1K OHM 5% 1/8W 0805 | R2, R13, R20, R23, R31, R35, R40, R43, R46, R49, R64, R71, R72, R73 | SMD-0805-RES | ERJ-6GEYJ102V | 14
100k | RES SMD 100K OHM 1% 1/8W 0805 | R3, R10, R16, R24, R29, R32, R65 | SMD-0805-RES | ERJ-6ENF1003V | 7
3.3k | RES SMD 3.3K OHM 1% 1/8W 0805 | R4, R25, R33 | SMD-0805-RES | ERJ-6ENF3301V | 3
20 | RES SMD 20 OHM 5% 1/2W 0805 | R5, R7, R26, R28, R34, R36 | SMD-0805-RES | ERJ-P06J200V | 6
10k | RES SMD 10K OHM 5% 1/2W 0805 | R6, R9, R11, R12, R21, R27, R37, R38, R41, R44, R47, R63, R70, R74 | SMD-0805-RES | ERJ-P06J103V | 14
1M | RES SMD 1M OHM 1% 1/8W 0805 | R8 | SMD-0805-RES | ERJ-6ENF1004V | 1
60.4 | RES SMD 60.4 OHM 1% 1/8W 0805 | R14, R15 | SMD-0805-RES | ERJ-6ENF60R4V | 2
0.0 | RES SMD 0.0 OHM JUMPER 1/8W 0805 | R17, R18, R19, R50, R52, R54, R56, R58, R60 | SMD-0805-RES | ERJ-6GEY0R00V | 9
30k | RES SMD 30K OHM 1% 1/8W 0805 | R39, R42, R45, R62 | SMD-0805-RES | ERJ-6ENF3002V | 4
330 | RES SMD 330 OHM 1% 1/8W 0805 | R48 | SMD-0805-RES | ERJ-6ENF3300V | 1
1 | RES SMD 1 OHM 1% 1/8W 0805 | R51, R53, R55, R57, R59, R61 | SMD-0805-RES | ERJ-6RQF1R0V | 6
200k | RES SMD 200K OHM 1% 1/8W 0805 | R66, R67, R68, R69 | SMD-0805-RES | ERJ-6ENF2003V | 4
OFF-mom push button SPST | OFF-mom push button SPST K12SCS1.55NOLFTX | S1 | K12SCS1.55NOLFTX | K12SCS1.55NOLFTX | 1
NCP21XM472J03RA | NTC THERMISTOR 4.7K OHM 5% 0805 | TH1, TH2, TH3 | SMD-0805-RES | NCP21XM472J03RA | 3
TP | SMD TEST POINT | TP1, TP2, TP5, TP6, TP7, TP8, TP9, TP10, TP12, TP13, TP18, TP21, TP24 | Test Point | TP | 13
MAX5063CASA+ | Half Bridge Based MOSFET Driver, 2A, BICMOS, PDSO8 | U1, U8, U9 | MAX5063DASA+ | MAX5063CASA+ | 3
INA281A1QDBVRQ1 | Operational Amplifier, 1 Func, 500uV Offset-Max, PDSO5 | U2, U10, U11 | SOT95P280X145-5N | INA281A1QDBVRQ1 | 3
TMUX1204DGSR | 5-V, 4: 1, 1-channel, general-purpose analog multiplexer 10-VSSOP -40 to 125 | U3 | TSSOP50P490X110-10N | TMUX1204DGSR | 1
NUCLEO-L432KC | BOARD NUCLEO STM32F303K8T6 | U4 | NUCLEO-L432KC | NUCLEO-L432KC | 1
ISO1050DWR | IC TXRX/ISO HALF 1/1 16SOIC | U5 | IL 41050TE | ISO1050DWR | 1
MAX5033CUSA+ | 500mA, 76V, High-Efficiency, MAXPower Step-Down DC-DC Converter | U6 | MAX5033CUSA+ | MAX5033CUSA+ | 1
ST715CR | High input voltage - 85 mA LDO linear regulator, SOT323-5L, Tape and Reel | U7 | ST715CR | ST715CR | 1
TL072CDR | IC OPAMP JFET 3MHZ 8SOIC | U16 | SOP127P600X175-8N | TL072CDR | 1
SN74AHC1G04DBVT | Inverter, AHC/VHC/H/U/V Series, 1-Func, 1-Input, CMOS, PDSO5 | U17, U20, U23 | SOT95P280X145-5N | SN74AHC1G04DBVT | 3
BU4S81G2-TR | AND Gate, 4000/14000/40000 Series, 1-Func, 2-Input, CMOS, PDSO5 | U18, U19, U21, U22, U24, U25, U26 | BU4S81G2 | BU4S81G2-TR | 7

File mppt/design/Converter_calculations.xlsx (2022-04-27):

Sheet: Multi_String_with_diode
Multiphase Boost Converter Design |  |  |  | Losses & Efficiency
Reference: | https://www.ti.com/seclit/wp/slup323/slup323.pdf |  |  | Total Power Loss (W): | 19.42346942
 |  |  |  | Estimated Efficiency: | 0.9778513622
System Specs |  | Other System Constraints |  | Component Selection & Losses
Solar Array Configuration |  | Switching Frequency: | 76000 | Inductor |  | FET |  | FET Driver |  | Rectifier Diode |  | Cin |  | Cout |  | MCU |  | Heatsink
Number || Strings: | 3 | Switching Frequency Per Phase: | 76000 | Allowable Ripple current pkpk | 3 | Boost FET RMS Current (A) | 4.210700654 | Part Number: | MIC4102 (https://www.digikey.com/en/products/detail/microchip-technology/MIC4102YM/771653) | P/N: | STPS4S200S (https://www.mouser.com/ProductDetail/STMicroelectronics/STPS4S200S?qs=BA62vJVifGo1urUInSDhRQ%3D%3D) | I_c_in_RMS (A) | 0.9114005769 | I_c_out_rms: | 2.849679357 | P/N: | Nucleo-Fk3038 | Max Ambient Temp C: | 45
String MPP Voltage: | 48.72 | Number phases: | 1 | Ballpark Inductor Value: | 0.0001052394737 | Sync FET RMS Current(A): | 4.274342055 | Alt Part 1: | MAX5063DASA+ (https://www.digikey.com/en/products/detail/analog-devices-inc-maxim-integrated/MAX5063DASA/1513485) | Alt Part: | TSP10H200S S1G (https://www.digikey.com/en/products/detail/taiwan-semiconductor-corporation/TSP10H200S-S1G/7360635) |  |  |  |  | Top current draw: | 0.3 | Target Max FET Junction Temp C: | 125
String MPP Current (A) | 6 | MPP Duty Cycle: | 0.4925 | IL Peak (Isat must be >): | 7.5 |  |  | Alt Part 2: | MIC4104YM |  |  |  |  |  |  | Vin | 12 | Permissible J/A temp diff: | 80
 |  | Assumed efficiency: | 0.95 |  |  |  |  | Alt Part 3: | MAX15019BASA+ |  |  |  |  |  |  |  |  | FET Power Dissipation (W): | 1.5978
Battery Configuration |  | Total Output power: | 833.112 |  |  |  |  |  |  |  |  |  |  |  |  |  |  | Largest Permissible thermal impedance: | 50.06884466
Battery Nominal Voltage: | 96 | Phase avg input current: | 6 | Component Specific Values |  | Component Specific Values |  | Component Specific Values |  | Component Specific Values |  | Component Specific Values |  | Component Specific Values
 |  | Phase output current: | 2.89275 | Part Number: | 74437529203101 (https://www.mouser.com/ProductDetail/Wurth-Elektronik/74437529203101?qs=f9yNj16SXrJ9N1gkF91A1Q%3D%3D) | Part Number: | IPP075N15N3 G (https://www.mouser.com/ProductDetail/Infineon-Technologies/IPP075N15N3-G?qs=mzcOS1kGbgcUKRttqIoCLg%3D%3D) | Source/Sink Current | 3 | Forward Voltage drop @ 6A | 0.85 | Part Number: |  | Part Number: | UCY2G101MHD6 (https://www.digikey.com/en/products/detail/nichicon/UCY2G101MHD6/2597737) |  |  | TIM Parameters:
Converter Input/Output |  |  |  | Inductance: | 0.0001 | RDSon (ohm): | 0.0072 | Quiescent Current: | 0.002 |  |  |  |  | Capacitance: | 0.001 |  |  | Thermal conductivity (W/MC): | 0.79
Mpp Vin: | 48.72 |  |  | DCR (Ohm): | 0.0229 | Gate Charge(Coul.) | 7e-08 |  |  |  |  |  |  | ESR: | 0.02 |  |  | Area of application (M^2) | 0.000112
Mpp Iin: | 18 |  |  | ISAT (A): | 9.4 | Switching Charge (Coul.) | 5.6e-08 |  |  |  |  |  |  | Ripple current rating: | 1.75 @ 100khz |  |  | Thickness of application (M) | 4e-05
Desired Vout: | 96 |  |  |  |  | Qoss(Coul.) | 1.79e-07 |  |  |  |  |  |  | Number capacitors: | 1 |  |  | Thermal Resistance Case/Sink (C/W): | 0.452079566
Pin | 876.96 |  |  | Resultant Values |  | Qrr | 4.78e-07
 |  |  |  | Ripple Current Pkpk: | 3.157184211 | Turn on time (S) | 1.866666667e-08
 |  |  |  | IL Peak (A): | 7.578592105 | Thermal coefficient JA (C/W): | 62 |  |  |  |  |  |  |  |  |  |  | Resultant Constraining Values:
 |  |  |  | IL_RMS(A): | 6.068826164 | Thermal coefficient JC (C/W): | 0.5 | Resultant Values |  | Resultant Values |  |  |  | Resultant Values |  | Resultant Values |  | Max heatsink Resistance Sink/Ambient (C/W) | 49.1167651
 |  |  |  | DCR Losses Per Phase (W): | 0.8434219082 | Maximum Junction Temp C: | 175 | IC Loss (Per driver) (W) | 0.3566304 | Avg Conduction Loss (per diode) | 2.4588375 |  |  | Total Capacitance: | 0.001 | Power Consumed | 3.6 | Max heatsink Resistance Sink/Ambient with rule of thumb for point load thermal connection (C/W) | 32.71176555
 |  |  |  | Total DCR Losses(W) | 2.530265724 |  |  | Total IC losses: | 1.0698912 | Total Conduction Loss: | 7.3765125 |  |  | Total ESR: | 0.02
 |  |  |  | Core + Winding Losses Per Phase(W): | 0.0178 | Resultant Values |  |  |  |  |  |  |  | V_c_out_Ripple: | 0.02045938452
 |  |  |  | Total Core Losses (W) | 0.0534 | Boost FET Condution Loss (W): | 0.127656 |  |  |  |  |  |  | I_C_out | 5.7
 |  |  |  |  |  | SyncFET Conduction Loss (W): | 0 |  |  |  |  |  |  | V_Cout_Ripple_ISR | 0.114
 |  |  |  |  |  | Total Conduction Losses (W): | 0.382968 |  |  |  |  |  |  | Vout_ripple (V) | 0.1158213556 |  |  | Component Specific Values
 |  |  |  |  |  | SW Transition Losses (Boost) (W): | 0.817152 |  |  |  |  |  |  |  |  |  |  | Part number: | 6396BG (https://www.digikey.com/en/products/detail/aavid-thermal-division-of-boyd-corporation/6396BG/1624741)
 |  |  |  |  |  | Total SW Transition Losses (W): | 2.451456 |  |  |  |  |  |  |  |  |  |  | Natural Convection Thermal resistance (C/W) | 5.6
 |  |  |  |  |  | Qoss Losses Per (All) FET: | 0.652992 |  |  |  |  |  |  |  |  |  |  | Rule of thumb 33% increase thermal resistance for point load thermal connection: | 7.448
 |  |  |  |  |  | Total Qoss Losses (W) | 1.958976
 |  |  |  |  |  | Qrr losses per (Boost) FET: (W) | 0
 |  |  |  |  |  | Total Qrr Losses:(W) | 0 |  |  |  |  |  |  |  |  |  |  | Resultant Values
Open Questions: |  |  |  |  |  |  |  |  |  |  |  |  |  |  |  |  |  | FET Junction Max Temp C: | 58.42164713
Why does boost FET incur QRR losses and not sync fet?
How to assess stability of system (gain/phase margin)
CCM vs DCM mode of operation advantages?

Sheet: Multi_String_Single_phase
Multiphase Boost Converter Design |  |  |  | Losses & Efficiency
Reference: | https://www.ti.com/seclit/wp/slup323/slup323.pdf |  |  | Total Power Loss (W): | 24.86302892
 |  |  |  | Estimated Efficiency: | 0.9716486169
System Specs |  | Other System Constraints |  | Component Selection & Losses
Solar Array Configuration |  | Switching Frequency: | 76000 | Inductor |  | FET |  | FET Driver |  | Cin |  | Cout |  | MCU |  | Heatsink
Number || Strings: | 3 | Switching Frequency Per Phase: | 76000 | Allowable Ripple current pkpk | 3 | Boost FET RMS Current (A) | 4.210700654 | Part Number: | MIC4102 (https://www.digikey.com/en/products/detail/microchip-technology/MIC4102YM/771653) | I_c_in_RMS (A) | 0.9114005769 | I_c_out_rms: | 2.849679357 | P/N: | Nucleo-Fk3038 | Max Ambient Temp C: | 45
String MPP Voltage: | 48.72 | Number phases: | 1 | Ballpark Inductor Value: | 0.0001052394737 | Sync FET RMS Current(A): | 4.274342055 | Alt Part 1: | MAX5063DASA+ (https://www.digikey.com/en/products/detail/analog-devices-inc-maxim-integrated/MAX5063DASA/1513485) |  |  |  |  | Top current draw: | 0.3 | Target Max FET Junction Temp C: | 125
String MPP Current (A) | 6 | MPP Duty Cycle: | 0.4925 | IL Peak (Isat must be >): | 7.5 |  |  | Alt Part 2: | MIC4103YM |  |  |  |  | Vin | 12 | Permissible J/A temp diff: | 80
 |  | Assumed efficiency: | 0.95 |  |  |  |  | Alt Part 3: | MAX15019BASA+ |  |  |  |  |  |  | FET Power Dissipation (W): | 5.085288
Battery Configuration |  | Total Output power: | 833.112 |  |  |  |  |  |  |  |  |  |  |  |  | Largest Permissible thermal impedance: | 15.73165571
Battery Nominal Voltage: | 96 | Phase avg input current: | 6 | Component Specific Values |  | Component Specific Values |  | Component Specific Values |  | Component Specific Values |  | Component Specific Values
 |  | Phase output current: | 2.89275 | Part Number: | 74437529203101 (https://www.mouser.com/ProductDetail/Wurth-Elektronik/74437529203101?qs=f9yNj16SXrJ9N1gkF91A1Q%3D%3D) | Part Number: | IPP075N15N3 G (https://www.mouser.com/ProductDetail/Infineon-Technologies/IPP075N15N3-G?qs=mzcOS1kGbgcUKRttqIoCLg%3D%3D) | Source/Sink Current | 3 | Part Number: |  | Part Number: | UCY2G101MHD6 (https://www.digikey.com/en/products/detail/nichicon/UCY2G101MHD6/2597737) |  |  | TIM Parameters:
Converter Input/Output |  |  |  | Inductance: | 0.0001 | RDSon (ohm): | 0.0072 | Quiescent Current: | 0.002 |  |  | Capacitance: | 0.001 |  |  | Thermal conductivity (W/MC): | 0.79
Mpp Vin: | 48.72 |  |  | DCR (Ohm): | 0.0229 | Gate Charge(Coul.) | 7e-08 |  |  |  |  | ESR: | 0.02 |  |  | Area of application (M^2) | 0.000112
Mpp Iin: | 18 |  |  | ISAT (A): | 9.4 | Switching Charge (Coul.) | 5.6e-08 |  |  |  |  | Ripple current rating: | 1.75 @ 100khz |  |  | Thickness of application (M) | 4e-05
Desired Vout: | 96 |  |  |  |  | Qoss(Coul.) | 1.79e-07 |  |  |  |  | Number capacitors: | 1 |  |  | Thermal Resistance Case/Sink (C/W): | 0.452079566
Pin | 876.96 |  |  | Resultant Values |  | Qrr | 4.78e-07
 |  |  |  | Ripple Current Pkpk: | 3.157184211 | Turn on time (S) | 1.866666667e-08
 |  |  |  | IL Peak (A): | 7.578592105 | Thermal coefficient JA (C/W): | 62 |  |  |  |  |  |  |  |  | Resultant Constraining Values:
 |  |  |  | IL_RMS(A): | 6.068826164 | Thermal coefficient JC (C/W): | 0.5 | Resultant Values |  |  |  | Resultant Values |  | Resultant Values |  | Max heatsink Resistance Sink/Ambient (C/W) | 14.77957614
 |  |  |  | DCR Losses Per Phase (W): | 0.8434219082 | Maximum Junction Temp C: | 175 | IC Loss (Per driver) (W) | 0.3566304 |  |  | Total Capacitance: | 0.001 | Power Consumed | 3.6 | Max heatsink Resistance Sink/Ambient with rule of thumb for point load thermal connection (C/W) | 9.843197712
 |  |  |  | Total DCR Losses(W) | 2.530265724 |  |  | Total IC losses: | 1.0698912 |  |  | Total ESR: | 0.02
 |  |  |  | Core + Winding Losses Per Phase(W): | 0.0178 | Resultant Values |  |  |  |  |  | V_c_out_Ripple: | 0.02045938452
 |  |  |  | Total Core Losses (W) | 0.0534 | Boost FET Condution Loss (W): | 0.127656 |  |  |  |  | I_C_out | 5.7
 |  |  |  |  |  | SyncFET Conduction Loss (W): | 0.131544 |  |  |  |  | V_Cout_Ripple_ISR | 0.114
 |  |  |  |  |  | Total Conduction Losses (W): | 0.7776 |  |  |  |  | Vout_ripple (V) | 0.1158213556 |  |  | Component Specific Values
 |  |  |  |  |  | SW Transition Losses (Boost) (W): | 0.817152 |  |  |  |  |  |  |  |  | Part number: | 6396BG (https://www.digikey.com/en/products/detail/aavid-thermal-division-of-boyd-corporation/6396BG/1624741)
 |  |  |  |  |  | Total SW Transition Losses (W): | 2.451456 |  |  |  |  |  |  |  |  | Natural Convection Thermal resistance (C/W) | 5.6
 |  |  |  |  |  | Qoss Losses Per (All) FET: | 0.652992 |  |  |  |  |  |  |  |  | Rule of thumb 33% increase thermal resistance for point load thermal connection: | 7.448
 |  |  |  |  |  | Total Qoss Losses (W) | 3.917952
 |  |  |  |  |  | Qrr losses per (Boost) FET: (W) | 3.487488
 |  |  |  |  |  | Total Qrr Losses:(W) | 10.462464 |  |  |  |  |  |  |  |  | Resultant Values
Open Questions: |  |  |  |  |  |  |  |  |  |  |  |  |  |  |  | FET Junction Max Temp C: | 87.71682382
Why does boost FET incur QRR losses and not sync fet?
How to assess stability of system (gain/phase margin)
CCM vs DCM mode of operation advantages?

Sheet: Library_Parts_To_Make
Power Inductor: (https://www.mouser.com/ProductDetail/Wurth-Elektronik/74437529203101?qs=f9yNj16SXrJ9N1gkF91A1Q%3D%3D) | 74437529203101 (https://www.mouser.com/ProductDetail/Wurth-Elektronik/74437529203101?qs=f9yNj16SXrJ9N1gkF91A1Q%3D%3D)
MOSFET: | IPP075N15N3 G (https://www.mouser.com/ProductDetail/Infineon-Technologies/IPP075N15N3-G?qs=mzcOS1kGbgcUKRttqIoCLg%3D%3D)
Gate Driver: | MAX5063DASA+ (https://www.digikey.com/en/products/detail/analog-devices-inc-maxim-integrated/MAX5063DASA/1513485)
Electrolytic Cap: | UCY2G101MHD6 (https://www.digikey.com/en/products/detail/nichicon/UCY2G101MHD6/2597737)
12V Regulator: | MAX5033CUSA+ (https://www.digikey.com/en/products/detail/analog-devices-inc-maxim-integrated/MAX5033CUSA/1513659)
10uF ceramic: | C3216X6S2A106K160AC (https://www.digikey.com/en/products/detail/tdk-corporation/C3216X6S2A106K160AC/14642034)
.1uF Ceramic: | CGA4J3X7T2E104K125AA (https://www.digikey.com/en/products/detail/tdk-corporation/CGA4J3X7T2E104K125AA/2672869)
1uF Ceramic: | GMC31X7R105K100NT (https://www.digikey.com/en/products/detail/cal-chip-electronics-inc/GMC31X7R105K100NT/12697998)
Buck Inductor: | SRR1260A-561K (https://www.digikey.com/en/products/detail/bourns-inc/SRR1260A-561K/4340231)
LDO: | ST715CR (https://www.digikey.com/en/products/detail/stmicroelectronics/ST715CR/13592617)
CAN Transciever: | IL 41050TE (https://www.digikey.com/en/products/detail/IL%252041050TE/390-IL41050TE-ND/2262662?curr=usd)

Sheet: Original_Multiphase
Multiphase Boost Converter Design |  |  |  | Losses & Efficiency
Reference: | https://www.ti.com/seclit/wp/slup323/slup323.pdf |  |  | Total Power Loss (W): | 40.47578213
 |  |  |  | Estimated Efficiency: | 0.9538453497
System Specs |  | Other System Constraints |  | Component Selection & Losses
 |  |  |  |  |  |  |  |  |  | Transitioned to multi string single phase design on different sheet. Primary reason was too high of switching losses at switching frequency needed to keep inductor in CCM. Higher inductance values could fix this by moving to lesser frequency (which is what we do on new design), but parts with inductance values with > 9A sat current are few, and we want options in supply shortage. IN addition, having seperate MPPT's per string allows for most efficienct MPPT tracking and prevention of false mppt peaks when combining multiple strings together if one is shaded.
Solar Array Configuration |  | Switching Frequency: | 450000 | Inductor |  | FET |  | FET Driver
Number || Strings: | 3 | Switching Frequency Per Phase: | 225000 | Allowable Ripple current pkpk | 4.5 | Boost FET RMS Current (A) | 6.316050981 | Part Number: | MIC4102 (https://www.digikey.com/en/products/detail/microchip-technology/MIC4102YM/771653)
String MPP Voltage: | 48.72 | Number phases: | 2 | Ballpark Inductor Value: | 2.369837037e-05 | Sync FET RMS Current(A): | 6.411513082 | Alt Part 1: | MAX5063DASA+ (https://www.digikey.com/en/products/detail/analog-devices-inc-maxim-integrated/MAX5063DASA/1513485)
String MPP Current (A) | 6 | MPP Duty Cycle: | 0.4925 | IL Peak (Isat must be >): | 11.25 |  |  | Alt Part 2: | MIC4103YM
 |  | Assumed efficiency: | 0.95 |  |  |  |  | Alt Part 3: | MAX15019BASA+
Battery Configuration |  | Total Output power: | 833.112
Battery Nominal Voltage: | 96 | Phase avg input current: | 9 | Component Specific Values |  | Component Specific Values |  | Component Specific Values
 |  | Phase output current: | 4.339125 | Part Number: | VER2923-223 (https://www.coilcraft.com/en-us/products/power/shielded-inductors/high-current-flat-wire/agp-ver/ver2923/ver2923-223/) | Part Number: | IPP075N15N3 G (https://www.mouser.com/ProductDetail/Infineon-Technologies/IPP075N15N3-G?qs=mzcOS1kGbgcUKRttqIoCLg%3D%3D) | Source/Sink Current | 3
Converter Input/Output |  |  |  | Inductance: | 2.2e-05 | RDSon (ohm): | 0.0072 | Quiescent Current: | 0.002
Mpp Vin: | 48.72 |  |  | DCR (Ohm): | 0.0026 | Gate Charge(Coul.) | 7e-08
Mpp Iin: | 18 |  |  | ISAT (A): | 14.7 | Switching Charge (Coul.) | 5.6e-08
Desired Vout: | 96 |  |  |  |  | Qoss(Coul.) | 1.79e-07
Pin | 876.96 |  |  | Resultant Values |  | Qrr | 4.78e-07
 |  |  |  | Ripple Current Pkpk: | 4.847393939 | Turn on time (S) | 1.866666667e-08
 |  |  |  | IL Peak (A): | 11.42369697
 |  |  |  | IL_RMS(A): | 9.108133856 | Resultant Values |  | Resultant Values
 |  |  |  | DCR Losses Per Phase (W): | 0.2156910661 | Boost FET Condution Loss (W): | 0.287226 | IC Loss (Per driver) (W) | 1.63212
 |  |  |  | Total DCR Losses(W) | 0.4313821321 | SyncFET Conduction Loss (W): | 0.295974 | Total IC losses: | 4.89636
 |  |  |  | Core + Winding Losses Per Phase(W): | 1.619 | Total Conduction Losses (W): | 1.1664
 |  |  |  | Total Core Losses (W) | 3.238 | SW Transition Losses (Boost) (W): | 3.6288
 |  |  |  |  |  | Total SW Transition Losses (W): | 7.2576
 |  |  |  |  |  | Qoss Losses Per (All) FET: | 1.9332
 |  |  |  |  |  | Total Qoss Losses (W) | 7.7328
 |  |  |  |  |  | Qrr losses per (Boost) FET: (W) | 10.3248
 |  |  |  |  |  | Total Qrr Losses:(W) | 20.6496

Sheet: POL_Power_Breakdown
Device: | P/N | # On board | Vin | Iin | Total Load (A) | Power Tree
NucleoSTM32 | NUCLEO-L432KC | 1 | 7 to 12 | 0.3 | 0.3 | Solar Array (57.12VOC)
Gate Driver |  | 3 | 12 | 0.004 | 0.012
CAN Transceiver |  | 1 |  |  |  | 12V Buck Converter
Isense Amp | INA240 | 7 | 2.7 to 5.5 | 0.0026 | 0.0182
Op Amp | TL072CDR | 4 | 0 to 36 | 0.002 | 0.008 | Nucleo (3.3V onboard converter)

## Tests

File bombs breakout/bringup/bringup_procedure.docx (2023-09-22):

THE FOLLOWING IS AN EXAMPLE FROM A POD V PCB.

Braking IO Rev A Bring Up Procedure

11/6/2019

Purpose

This document is designed to list the steps required to bring up the Rev A Braking IO PCBs.

Initial Inspection and Continuity Checks

1. Check packaging for any visible damage from shipping.
2. Open package and verify 5 bare PCBs arrived
3. Inspect the board for any visual defects, including poor soldermask, damaged pads, etc.
4. Check power rails
  a. On each IC, verify VCC and GND are present on the appropriate pad
  b. Verify power rails are not shorted together
  c. Verify power rails are not shorted to GND
    i. V-BUS
    ii. V-POS7V
    iii. V-POS5V
    iv. V-POS3V3
5. Check for undrilled vias and through holes
6. Check for any shorted pads or traces

Solder Paste

1. Ensure you have a fresh, refrigerated tube of solder paste
2. If desired, laser cut a sheet of mylar
3. Apply solder paste to each pad
  a. Avoid applying too much solder paste
  b. Avoid applying too little solder paste

Organizing Components

1. Organizing components beforehand can be a huge timesaver when doing assembly by hand. I recommend splitting your components into groups (resistors, capacitors, ICs, etc and arrange them in alpha-numeric order.
  a. This set of components was a self-contained digikey order, so if should be easier to find what you need.
2. Print off a copy of a BOM (and Schematics if desired)
3. Make sure you check the schematic for DNP components, If a component is DNP, that means DO NOT POPULATE! This could be done for a number of reasons like configuration options, addressing, or flexibility.

Place SMD Components

1. It is recommended to place the power supply components first and verify the supplies are functional before placing the rest of your components. Remember, boards are cheap, components are expensive.
2. Reflow components using an oven (preferred) or a hot air tool, reflow your components
  a. Inspect the board after to make sure all solder joints were reflowed
  b. Inspect the board after to make sure there are no shorts
  c. If necessary, populate a 24V header so you can power on the initial supplies
3. Performing continuity checks, especially on your power rails and when everything is as expected, power on the board and verify all of the power rails are coming up appropriately
  a. Be sure to set the power supply to 24V and 500mA current limit
4. Fill in the table after powering on the board

Rail | Expected | Actual
V-BUS | 24V (Power supply)
V-POS7V | 7V +/- 2%
V-POS5V | 5V +/- 2%
V-POS24V | 24V +/- 1%
V-POS3V3 (After Nucleo populated) | 3.3V +/- 2%

5. After power supplies are placed and verified, place the rest of the SMD components
  a. Note, only place one of the solenoid driver circuits and verify that circuit is working before placing the rest of the ICs
6. Reflow components, as before
7. Inspect and touch up any open circuits or shorts

Place Through Hole Components

1. Almost there! Solder your through hole components to the board
2. Perform one last continuity check on the power rails

Power on the Board!

1. Set a current limit on the supply.
2. Connect the board to power
3. Be prepared to power off the supply in the event of a short circuit (indicated by either hitting the current limit or magic smoke coming off of the board)

Verify Sub-Circuits

Some circuits can be tested more easily than others. Below is a recommended test procedure

Tests that can be performed without software support:

1. Voltage telemetry on all rails (Measure the output of the Op-Amp and verify it corresponds to the actual measurement)

Rail | Expected Range | Measured Value
V-BUS | 1.82V-2.54V
V-POS7V | 4.1V-4.2V
V-POS5V | 3.9V-4.0V
V-POS24V | No Telem

2. Current Telemetry on all rails (Measure on the output of the INA240x)

Rail | Expected Range | Measured Value
V-BUS | 4.0V Max
V-POS7V | 4.0V Max
V-POS5V | 4.0V Max
V-POS24V | No Telem

3. Verify Pressure Sensor Circuit
  a. This is a lower priority circuit to test, as it’s a direct copy from Pod IV
  b. Connect a pressure sensor to P12 and verify the output is appropriate.
  c. Bonus: Connect to a pressurized system

Sensor Number | Sensor Type | Expected Vout | Measured Vout

4. Verify Temperature circuit
  a. Similar to the pressure sensor circuit, verify the output voltage is appropriate for the thermistor.
  b. Verify the voltage changes with temperature

Expected Vout @ Room Temp | Measured Vout @ Room Temp | Expected Vout @ 40C | Measured Vout @ 40C

5. Verify Retroreflective Circuit
  a. Connect a retroreflective sensor to the header
  b. Flash a retro tape and confirm:
    i. LED output changes
    ii. Voltage changes on the negative edge

Retro Number | Pass?
1
2

6. Verify Solenoid Driver Circuit
  a. Connect a solenoid to the solenoid header
  b. Drive the solenoid EN signal (Either manually, or via controls if they are ready)
  c. Ensure that the solenoid is driven
  d. Measure how power consumption

Solenoid Number | Actuates? | Unactuates? | Nominal Power Consumption | Max Power Consumption
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
7. Verify Watchdog Circuit
  a. Watchdog design must be completed first
8. Verify I2C Devices
  a. Relies heavily on controls
  b. I2C Scan can be implemented through MBED OS
9. Verify UART Circuit

Note: The STM32L432KC has a quick and dirty compiler called MBED OS that you can write quick programs to test hardware functionality of the microcontroller. Production code won’t necessarily use this, but verifying hardware is important. Remember, the goal of the document is to have the firmware engineers not able to blame all of the troubles on hardware issues! If you can verify with MBED, you can likely say “sounds like a firmware issue”

Debugging

Some general tips on circuit debugging:

1. Thou shall check voltages
  a. Seriously, 95% of issues for projects like this are either an unplugged power supply, disabled power supply
2. Thou shall understand what circuit you are trying to test
  a. Is it really borked? Or do I just not understand what’s actually going on? Re-read your datasheet, pull up the schematic
3. Thou shall check continuity
  a. Go around all of the pins for your IC and verify they are connected properly. In my experience, it could be a bad lead, bad solder connection, or even a misspelled net name on your schematic. Don’t fret, you can always bluewire low current connections you might be missing!
  b. Also make sure you have placed all of the components. Last year we were plagued by missing 0-ohm resistors or other configurations
4. Thou shall check voltages
  a. See 1

Congrats

If you’ve made it this far, you should have a completed, functional, non-buggy PCB!

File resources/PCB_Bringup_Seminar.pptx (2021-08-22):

## PCB Bring-up Seminar

2/14/2019 & 2/15/2019
Ryan Castle

## Objectives / Questions to Answer

- Developing Production Hardware
- Where do I find information to build a board?
- What Atlium tools do I need to know how to use?
- What materials do I need?
- Soldering 101
- Build up test PCBs

## End Goal

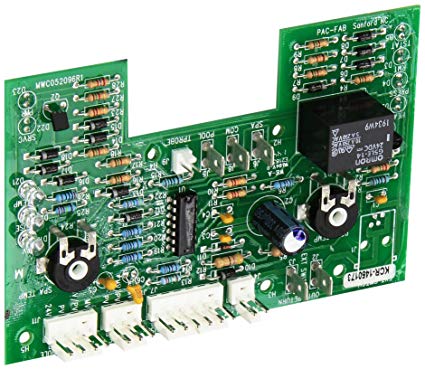
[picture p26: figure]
Image result for circuit board

- Functional Circuit Board capable of going into the pod
  - Populated PCBs
  - Soldering components is only ½ of the task
  - Bring-up instructions include basic testing information
- Be able to blame issues on the software and controls team

## Disclaimer

- We’ve spent a lot of time designing these PCBs and have spent ~$800 on components (~$2000 including sponsored components/PCBs)
- If you aren’t sure, ask
  - Definitely possible a mistake was made in schematic design or layout
- Practice on a test PCB
- Follow bring up instructions closely
- Inspect, inspect, inspect before you power on
  - No boards should be powered on for the first time without approval from Ethan or Ryan
  - Magic Smoke
- Mistakes are ok, we just want to avoid them
- Material might be really boring if you’ve done this before

## Altium Repository

- https://github.com/badgerloop-software/podiv-altium
- Primary source for all PCB information
- Possible to build a board from outputs
  - However, cloning the repo can speed up process
- Schematics, Layout files
  - Podiv-Altium/board_release/<pcb_name>/<revision_letter>/output/<*SCH*>
- Bringup Documentation
  - Podiv-Altium/bringup/<pcb_name>/<pcb_name>_bringup.docx

## Altium Tools

- Search for a Reference Designator (R1, U3, LED2)
  - In Schematics: <CTRL> + <F>
  - In Layout: <J>+<C>
- More information on a component
  - In Schematic:
    1. Double click on Component and the properties window will appear
    2. Click on the Properties Tab
    3. Manufacturer, P/N, Digikey P/N, link will appear.
    - Disclaimer: Sometimes, the parts to be populated won’t match with what’s in the schematic. This is because sometimes 2 components will have the same footprint or a BOM change was required for part availability

## Material Required

- See Bring-up Documentation
- Example for Ideal Diode PCB:
  - P4_LV_IdealDiode_001_REVA PCBs
  - Soldering iron
  - Solder
  - Solder Paste
  - Side cutters (snips)
  - PCB BOM
  - Oven

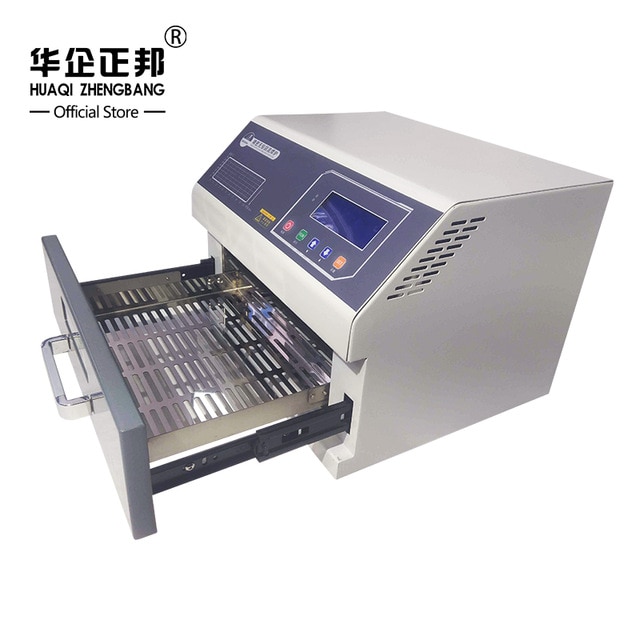
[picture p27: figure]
Image result for solder oven

## SMD Soldering

- https://mediaspace.wisc.edu/media/ECE370PowerSupplySM2-DVD/0_qaluf0im
  - Courtesy of Mark Allie, ECE 370
- Check Oven Settings
  - For this seminar, see if other groups are almost ready to use the oven. Possible to do multiple boards at once.

## What do I do if I find a problem with a board? Feature Request?

- Possible Answers:
A. Scream
B. Shout
C. Ignore it and hope it will go away
D. Submit a Feature Request or Bug Report on Github

Answer: All Except C
https://github.com/badgerloop-software/podiv-altium/issues

## Bring-up PCBs

- 2-3 people per PCB
- Boards:
  - Test PCBs (x2)
  - Processor (x5)
  - Ideal Diode (x2)
  - High Voltage Battery Breakout (x6) (Through Hole Only)
- Parts are all in the Digikey Box
  - Probably going to be a bottle neck. Be patient

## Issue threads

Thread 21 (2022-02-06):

MPPT Rev 2 Updates

dawiggleman, 2022-02-06:
List of bugs/improvements to make for MPPT Rev 2

dawiggleman, 2022-02-06:
Output Electrolytic Caps:

Problem:
The hole sizes for component UCY2G101MHD6 are too small to insert the pins of the capacitors into. Make holes in this footprint larger and update schematics/layout.

Temporary Solution:
File down leads to fit holes, or cut the leads short, put thin wire through the holes and solder to the capacitors. Hot glue capacitors down.

dawiggleman, 2022-02-06:
Board size:

Consider placing LV components on the bottom side of the board to get under the 30 sq. inch requirement for advanced circuits to get $66 four layer boards.

dawiggleman, 2022-02-06:
Overvoltage protection:

Add an overvoltage protection circuit to prevent discharge over a certain voltage. Would consist of a zener diode, schmitt trigger, and any additional logic to turn the gate drivers off.

dawiggleman, 2022-02-06:
Addition of pi filter to solar inputs:

Adding a pi filter configuration could reduce the current ripple on the input of the boost strings. This would allow for better operation at the exact maximum power point over the course of a switching cycle, instead of having variation about the mpp while current is being drawn from the array.

dawiggleman, 2022-02-11:
Replace CAN driver with ISO1050DWR:

ISO1050DWR is available at an upcharge on resaler's sites. Ordered 11 for future use.

On Rev 1 board: use this chip, but need to deadbug TX/RX pins to be correct, but every other pin on the footprint should be compatible.

dawiggleman, 2022-02-12:
The 1uF 100V capacitors used were PN/s that required you to order in quantities of 2000+. Replace with https://www.digikey.com/en/products/detail/kemet/C1206C105K1RAC7800/5119820. This part has already been added to inventree.

dawiggleman, 2022-02-13:
R22 (Feedback resistor to LDO 249K needs to be replaced with 31k). Replaced w/ 30k on current board.

dawiggleman, 2022-02-23:
Put power schottky diode in parallel with Sync FETS on boost converters to increase efficiency. Schottky diodes will remove the reverse recovery losses felt by the boost FET. QRR losses are about half our losses (11W), with the diode, the primary loss will be V*I losses, and this will be about half (6W) of average losses due to the high side switch.

Component options:
https://www.digikey.com/en/products/detail/taiwan-semiconductor-corporation/TSP10H200S-S1G/7360635
https://www.mouser.com/new/stmicroelectronics/stm-stps4s200-rectifiers/

dawiggleman, 2022-03-06:
Add discharge resistors across input capacitors to 12V buck converter

dawiggleman, 2022-03-06:
Make output connector unique and different from solar strings with on -board anderson connector:
https://www.digikey.com/en/products/detail/anderson-power-products,-inc./ASMPR45-1X2-RK/13150596?utm_adgroup=Essen%20Deinki&utm_source=google&utm_medium=cpc&utm_campaign=Shopping_DK%2BSupplier_Other&utm_term=&utm_content=Essen%20Deinki&gclid=CjwKCAiAyPyQBhB6EiwAFUuakrL7xmNcBOnO0dT_TqeadtABZVygj-zTtNgWkxix_3Iy7FF08XfuRBoCRKQQAvD_BwE

dawiggleman, 2022-03-07:
Add dead time circuit:
Turns out the MAX5063DASA does not have a dead time circuit built in, the MAX5064 does. Add a dead time circuit to avoid shoot through on FETs.

Not immediately necessary if first choice for conversion is rectifier diodes, but will be good to have this option for future experiments.

dawiggleman, 2022-03-07:
> R22 (Feedback resistor to LDO 249K needs to be replaced with 31k). Replaced w/ 30k on current board.

dawiggleman, 2022-03-09:
Components to make in altium:
100uF UCY2G101MHD6 capacitor footprint change

ISO1050DWR: https://www.digikey.com/en/products/detail/texas-instruments/ISO1050DWR/2596853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

10uH inductor: https://www.digikey.com/en/products/detail/w%C3%BCrth-elektronik/7443251000/3476749

150V zener diode:https://www.digikey.com/en/products/detail/vishay-general-semiconductor-diodes-division/BZG03C150-HM3-08/7898703

Power Schottky Diode: https://www.digikey.com/en/products/detail/taiwan-semiconductor-corporation/TSP10H200S-S1G/7360635

Add 1uF 100V capacitor:https://www.digikey.com/en/products/detail/kemet/C1206C105K1RAC7800/5119820

Unique output connector: https://www.digikey.com/en/products/detail/anderson-power-products,-inc./ASMPR45-1X2-RK/13150596?utm_adgroup=Essen%20Deinki&utm_source=google&utm_medium=cpc&utm_campaign=Shopping_DK%2BSupplier_Other&utm_term=&utm_content=Essen%20Deinki&gclid=CjwKCAiAyPyQBhB6EiwAFUuakrL7xmNcBOnO0dT_TqeadtABZVygj-zTtNgWkxix_3Iy7FF08XfuRBoCRKQQAvD_BwE

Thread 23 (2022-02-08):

DriverIO schematic review

dawiggleman, 2022-02-08:
- Add title page with title and Revision number
- Add titles and engineers to each schematic
- Annotate schematics for individual component reference designators instead of having R?
- Add No ERC directives on pins without connections

Why is I2C_SDA and SCL attached to address pins?
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
Instead of using 0 ohm for address pin configuration, use 10k. This prevents a short if two are both accidentally populated
Put pullup resistors above the pulldown configuration resistors for easier readability

Ope. Make this page 1 in the project settings:
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

Why are SDA and SCL optionally tied to 3.3 here?
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

Connect enable pin to correct voltage or leave note if it's supposed to be floating:
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

Same as mainIO: is the forward voltage drop of the led > 1.6V? If not resistor needs to be bigger
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

Where does Driver screen attach to? Make obvious with a note of how that interfaces with system

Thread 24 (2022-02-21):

HV Controller PCB Review

ryanbear22, 2022-02-21:

dawiggleman, 2022-02-21:
- In future, do all work on branches so merge conflicts can be caught prior to pushing to main
- Looks like the green violations remaining on the board are height constraints of your 3D bodies. Change this rule to a higher value or an actual constraint if we have one

Spread out these vias a little more if you can, otherwise you have thin paths for current to get to the middle vias
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

Are you aware the DCDC converter footprint does not have holes? Right now there are just exposed copper:
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

While you're at it, double check the hole spacing on this footprint. Need to get it right or the whole board is unusable.

dawiggleman, 2022-02-21:
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
Make this VRAW_12 trace as wide as the rest of the trace

Make connectors flush with edge of board:
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

Put board info in this space in silkscreen (Name, board title, revision, badgerloop logo, altium logo)
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

The diodes footprints you're using don't have polarity indicators on them. Add them for assembly:
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

Tbh your vias look pretty large. Check out my mppt board to see what hole/annular ring size I'm using. Then all can be changed at once by selecting one, then right click "select similar objects" and you edit dimensions there:
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

Secondary thoughts on these footprints. We could just use solder paste and put the board in an oven for assembly. It will save additional complexity of this footprint and cost of adding vias in pad.

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

dawiggleman, 2022-02-21:
Minor detail but make these diodes even if you can:
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

Can probably hide silkscreen for mount holes:
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

Instead of making a right angle junction like this, just route from one pad to another, then route out from that second pad:
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

Get rid of this acute angle by routing to the left straight left out of the pad instead of at an angle:
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

Route straight out of the pad here:
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

On the traces coming out of the resistors here, have the trace come out as perpendicular to the hole as possible:
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

dawiggleman, 2022-02-21:
Last note: We need to add a "board outline". I think the best way to do it is to draw a line around the edge of the board on mechanical layer 4. It's just the black line around the edge of the board. Here's how I did it in MPPT:
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

See "M4" in the Layer set manager:
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

ryanbear22, 2022-02-26:
pushed with all changes added

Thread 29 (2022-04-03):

Battery Capacity Tester Rev A reworks

jacob3457, 2022-04-03:

verichjack, 2022-04-03:
Relay Pinout: pins 3 and 4 need to be switched and their traces rerouted.
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

jacob3457, 2022-04-03:
**R10 Change to Capacitor (Optional)**
May use a capacitor in circuit in place of R10 to reduce noise

verichjack, 2022-04-03:
Changing U1 and U2 from Texas Instruments IC OPAMP JFET 2 CIRCUIT 8SOIC to Texas Instruments TLC272C OPAMP

verichjack, 2022-04-03:
Switched the inverting and noninverting inputs pins 5 and 6.
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

verichjack, 2022-04-03:
Shunt Voltage and Current Set Scaled switched corresponding to pins 2 and 3.

verichjack, 2022-04-03:
Pad 2 for VR1 potentiometer moved to ground
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

jacob3457, 2022-04-03:
**UVLO Input change**
Need to connect the relay common net to the input to the UVLO op amp (now switched to the inverting input, see other comment), instead of BATT_POS_PROT. The op-amp needs to read the battery voltage before the relay, not after.
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

jacob3457, 2022-04-03:
**Possible Change-Move TH1**
Could move TH1 down on the board to be closer to the hole in the battery holder that it will go through.

jacob3457, 2022-04-03:
**Possible Change-Move Charging Chip**
Could move charging chip to allow for bigger heat sink.

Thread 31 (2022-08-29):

Temperature Monitor Schematic Review

ryanbear22, 2022-08-29:
Couple things to complete before it's ready to be ordered

1.  For some reason the netlist didn't seem to import correctly so try importing changes again

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

2. Run a Design Rule Check under Tools bar and fix anything that is reported

3. If using vias for ground make sure to create ground plane on the bottom

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

4. Resize board to remove unused space

5. Put board info in this area in silkscreen (Name, board title, revision, badgerloop logo)

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

ryanbear22, 2022-08-29:
Last note: We need to add a "board outline". I think the best way to do it is to draw a line around the edge of the board on mechanical layer 4. It's just the black line around the edge of the board. Here's how it was done for the MPPT:
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
See "M4" in the Layer set manager:
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

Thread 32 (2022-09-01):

High Voltage Rev B changes

ryanbear22, 2022-09-01:
This issue will be tracking any changes necessary to the PCB

ryanbear22, 2022-09-01:
Check the size of the vias used in Rev A I think dimensions were 30mil for the diameter and 15 mil for the hole size, but I would verify this and change all of the vias on Rev B

ryanbear22, 2022-09-01:
Have the connectors be flush with the edge of the board
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

ryanbear22, 2022-09-01:
We want to reduce the "rats nest" of traces as much as possible. The pins on the connector can be reordered to make routing easier, you just need to change them in the schematic first
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

ryanbear22, 2022-09-01:
The output of the DCDC Converter can max out at 15A and the copper traces can only handle a certain amount of power. This website calculates the thickness of the copper traces based on current https://www.4pcb.com/trace-width-calculator.html
Similar to Rev A we're going to need thicker traces for that 12V line that's going through the powerpath controller to the output from both the supplemental input and the DCDC converter
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

ryanbear22, 2022-09-01:
Same thing for anything HV it's not necessary but it's nice having thicker traces / polygons for anything that's high power to reduce the heat
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

ryanbear22, 2022-09-01:
In general we want to avoid having really long traces. Try getting creative with placement of components to avoid this or use vias sparingly to tidy traces like these up

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

ryanbear22, 2022-09-01:
if you go under **Tools > Design Rule Check > Run Design Rule Check** you'll see there's a lot of errors relating the size constraints. Try editing the rules under **Design > Rules** to resolve these errors

gerosar-tech, 2022-09-01:
Fixed trace by D12/D8

gerosar-tech, 2022-09-01:
Fixed traces by P1

gerosar-tech, 2022-09-01:
Made contactors flush with board edge

gerosar-tech, 2022-09-01:
Fixed acute angle

gerosar-tech, 2022-09-01:
Changed via sizes

ryanbear22, 2022-09-03:
remove any unnecessary vias, they should only be used when going from top to bottom layer. also there's still a couple that need to be resized

ryanbear22, 2022-09-03:
I would still to reduce the lengths of some traces, I think the HV-MC-IN to HV-MC-OUT path can be reduced by grouping components closer, currently that path goes back and forth across half the board.

the main branch still has the rev A pcb so that's always a good reference that can be used

gerosar-tech, 2022-09-06:
shortened those traces and checked via sizes

ryanbear22, 2022-09-06:
For the test points I actually missed something in the schematics see how TP18 has the circle to show it's connected but TP19 doesn't, play around with the pins to get the remaining test points connected
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
I have a feeling it's all of these since the pcb prj isn't throwing any errors about them not being connected to the correct net labels
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

After that's all resolved let's used test points instead of vias. This makes testing easier since we can include in the testing procedure what test point to be probing instead of having to reference the pcb layout in altium to make sure it's the right one.

ryanbear22, 2022-09-06:
could you try to recreate the layout of the Rev A powerpath, we need those oversized traces since there can be upwards of 15A going through those lines and the mosfets
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

gerosar-tech, 2022-09-07:
fixed the resistor that wasn't connected right

gerosar-tech, 2022-09-07:
fixed the test point connections that weren't actually made

gerosar-tech, 2022-09-07:
fixed ppc trace issues

gerosar-tech, 2022-09-07:
still need to put in more testpoints to replace deleted pads

ryanbear22, 2022-09-07:
swap connectors
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

ryanbear22, 2022-09-07:
rotate mosfets 180 degrees
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

ryanbear22, 2022-09-07:
move all high powered traces to top layer
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

ryanbear22, 2022-09-07:
make consistent large thickness
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

ryanbear22, 2022-09-07:
make traces consistent width where appropriate

ryanbear22, 2022-09-07:
revert mosfet back to relay :(

gerosar-tech, 2022-09-09:
swapped connectors

gerosar-tech, 2022-09-09:
rotated mosfets

gerosar-tech, 2022-09-09:
moved high power to top

gerosar-tech, 2022-09-09:
made consistent traces

gerosar-tech, 2022-09-09:
changed back to relay

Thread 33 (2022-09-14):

Driver IO Rev B Review

ryanbear22, 2022-09-14:
Tracking any changes for Rev B here

ryanbear22, 2022-09-14:
if you go under Tools > Design Rule Check > Run Design Rule Check you'll see there's a lot of errors relating the size constraints. Try editing the rules under Design > Rules to resolve these errors. Looks like most of the errors have to do with rules that can be changed under Design -> Rule Wizard. Might be worth comparing the Rev A rules

ryanbear22, 2022-09-14:
remove any acute angled traces
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

ryanbear22, 2022-09-14:
acute here too
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

lmaddox28, 2022-09-18:
These LEDs and headers need to be labeled on the silkscreen. What does the LED indicate? What does each connector pin connect to?

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

lmaddox28, 2022-09-18:
A bit tight right here on U1 & R13. You can see that the R13 silkscreen is a bit too close, and the U1 silkscreen is not very close to the actual component. I would re-route according to the blue annotations in this screenshot and try to move U1 to the top left hand corner. I may add more on this ADC layout in another comment.

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

lmaddox28, 2022-09-18:
P10 silkscreen is off of the PCB:
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

lmaddox28, 2022-09-18:
This RPi silkscreen outline has a plethora of violations--including being off the board:. I would look at what Rev A did here (either it was deleted or modified):
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

lmaddox28, 2022-09-18:
These headers are pretty close. If we are attaching alligator clips to them, we will be in danger of shorting GND & power, or power line to power line. The more relief we can add between these, the better:
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

lmaddox28, 2022-09-19:
All of the connectors need to have text labels describing what they connect to. See Main IO for reference:
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

ryanbear22, 2022-09-19:
> This RPi silkscreen outline has a plethora of violations--including being off the board:. I would look at what Rev A did here (either it was deleted or modified): 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

was a second outline added to resolve this?
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

lmaddox28, 2022-09-19:
I would change all of the silkscreen labels to 7.5mil stroke width. 30 mil text height should be enough to be legible, but if we go that small we want to decrease the width for clarity. See the difference below, where R32 has been changed to 7.5 mil. This change can be done fairly easy--as seen below, right click on one of them & then select "Find Similar Objects" and select "Same" for Text Height & Text Width. Apply --> Ok & then change them to 7.5mil in the properties panel that pops up.
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

lmaddox28, 2022-09-19:
One thing we want to keep in mind if our ADC signals have poor resolution is to add in a voltage reference to the circuit. It doesn't seem like we are utilizing it right now. Unfortunately this isn't something we can test until we get the actual signal.
We should probably add the voltage reference to this revision so the PCB has the pads for it in case we want it. We don't want this to be the only thing that makes us order a Rev C.
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

lmaddox28, 2022-09-19:
It is unclear to me why we would give ourselves the option to attach 3.3V power and the I2C lines to the analog inputs, and I couldn't find any clarification on Confluence. Lets get an answer to this question before ordering
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

lmaddox28, 2022-09-19:
A couple things on the ADC layout: (1) It would be nice to space things out a bit so that the components are easier to populate. (2) as Cooper mentioned, with a ton of capacitors and resistors next to each other, its nice for the capacitors to be orientated vertically and the resistors horizontally--with this circuit, there is a large mix of it:
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

lmaddox28, 2022-09-19:
To decongest the bottom part of the PCB and allow for the headers to be spaced out more (along with the other circuits), I would recommend moving either the headers or the UART transceiver to the space up here.
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

lmaddox28, 2022-09-19:
Related to the comment above: you can just move everything up a little bit, since there is empty space above too.
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

lmaddox28, 2022-09-19:
If you swapped the regulator & the INA chip, you would not have these bottom layer traces having to do a U shaped path to get to the RPi.

lmaddox28, 2022-09-19:
C36 should be in line with C33, C34, C35. Together they should be as close to the ICs Vin pin as possible. This means, move R60 down and turn it horizontal to allow for the caps to get as close as possible. This was, the input into the chip is as filtered as possible (bypass caps should also be as close as possible to the Vin pin).
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

lmaddox28, 2022-09-19:
This isn't mission critical, but another best practice to ensure that population goes as planned. Put the IC silkscreen labels in the same corner and orientation as the IC is. That way, there is no confusion as to which way the chip goes. I've marked some examples here, but it applies to all of them:
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

lmaddox28, 2022-09-19:
Recall what Cooper said about the Kevlin Connections for the shunt resistors. For the 12V, notice that the pad being used for PresShunt12V is the pad on the fuse, not the resistor. This will result in a poor reading:
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

For the 5V resistor, the pad being probed is from L3, not R49:
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

lmaddox28, 2022-09-19:
Before trying to rearrange entire circuits, I would recommend routing these DIO signals orthogonally. This will free up a lot of room to work with--you won't have to maneuver around these diagonals.
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

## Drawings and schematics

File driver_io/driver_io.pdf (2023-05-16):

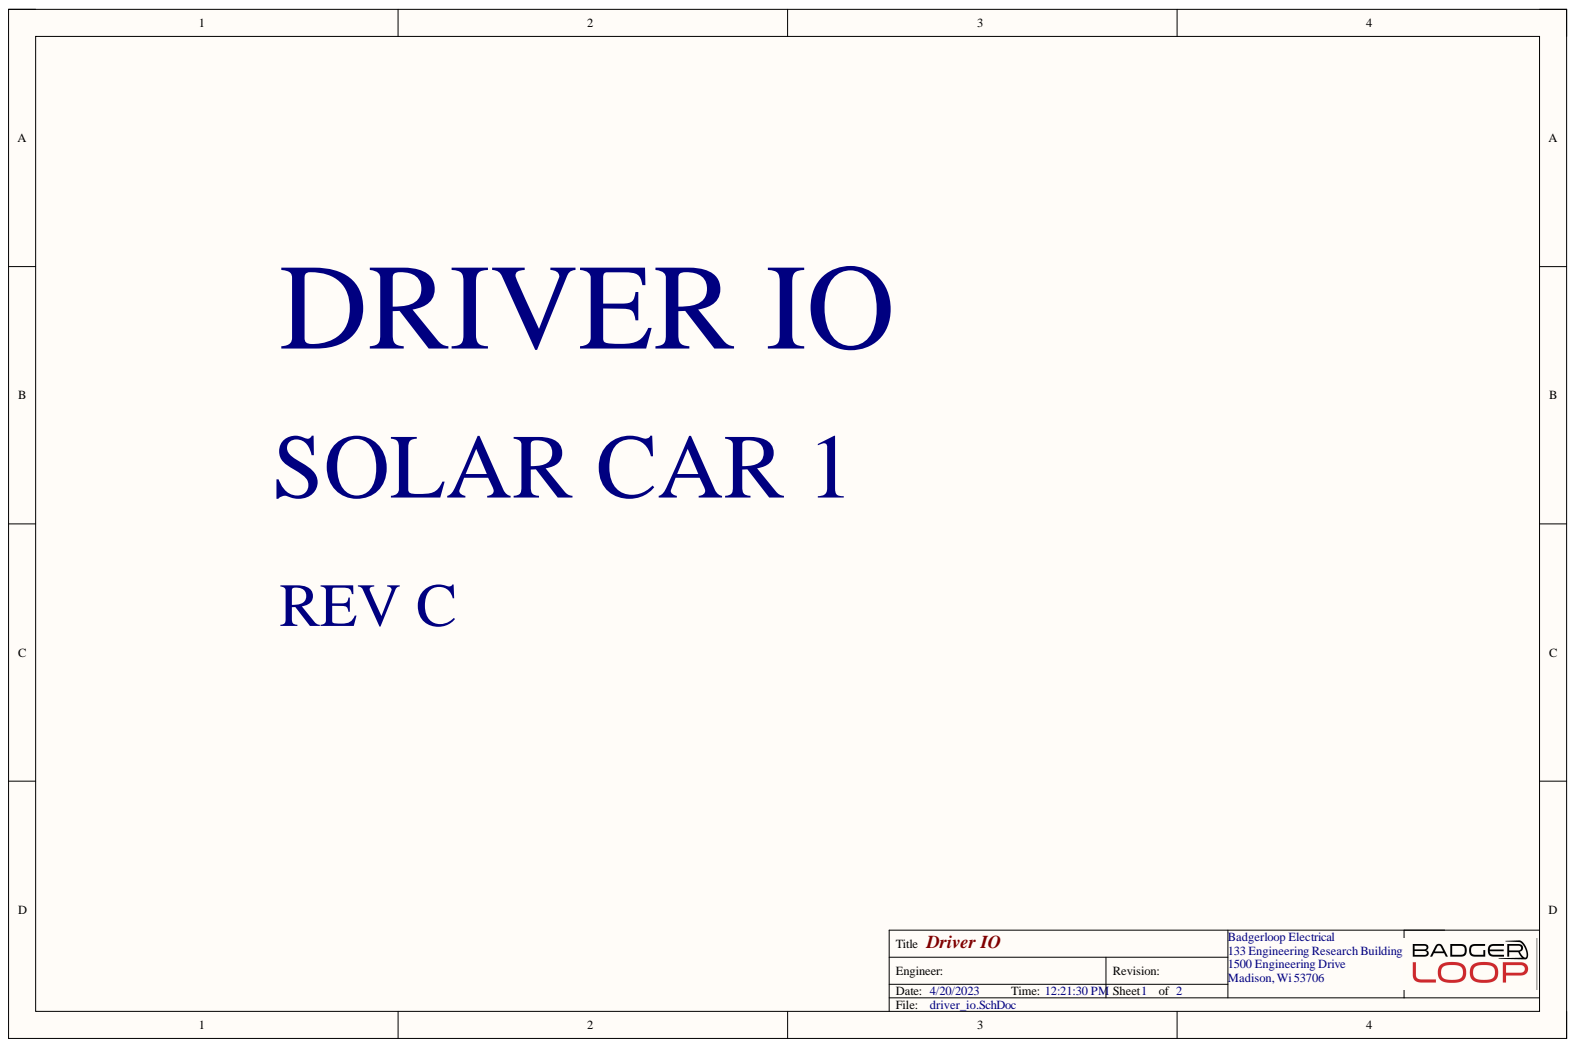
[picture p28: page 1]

Driver IO Title | Badgerloop Electrical 133 Engineering Research Building 1500 Engineering Drive Madison,Wi 53706

Engineer: | Revision:
Date: 4/20/2023 Time: 12:21:30 PM | Sheet 1 of 2

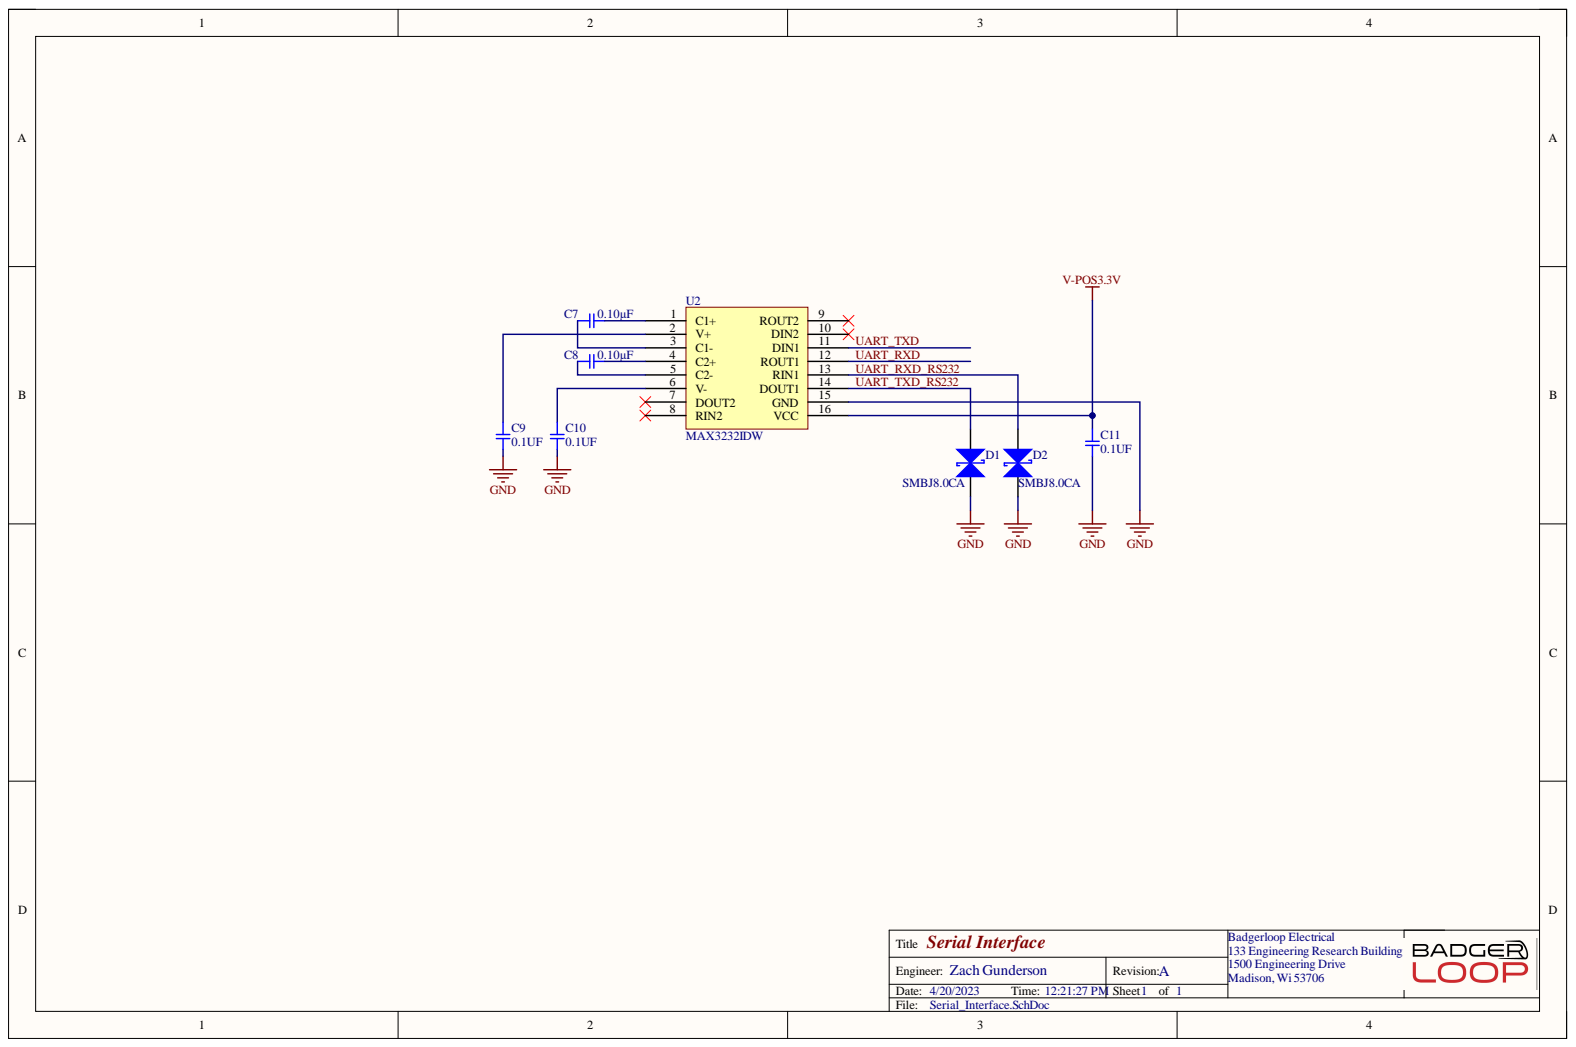
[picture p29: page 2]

Serial Interface Titl e | B adge rloop Ele ctri c a l 133 Engine e ring R ese a r ch Buildi n g 1500 Engine e ring Dr iv e Madison, Wi 5370 6

Zach G u n der s o n Engine e r : | A R evision :

Da te : 4/20/202 3 Time : 12:21:27 P M | She e t 1 o f 1

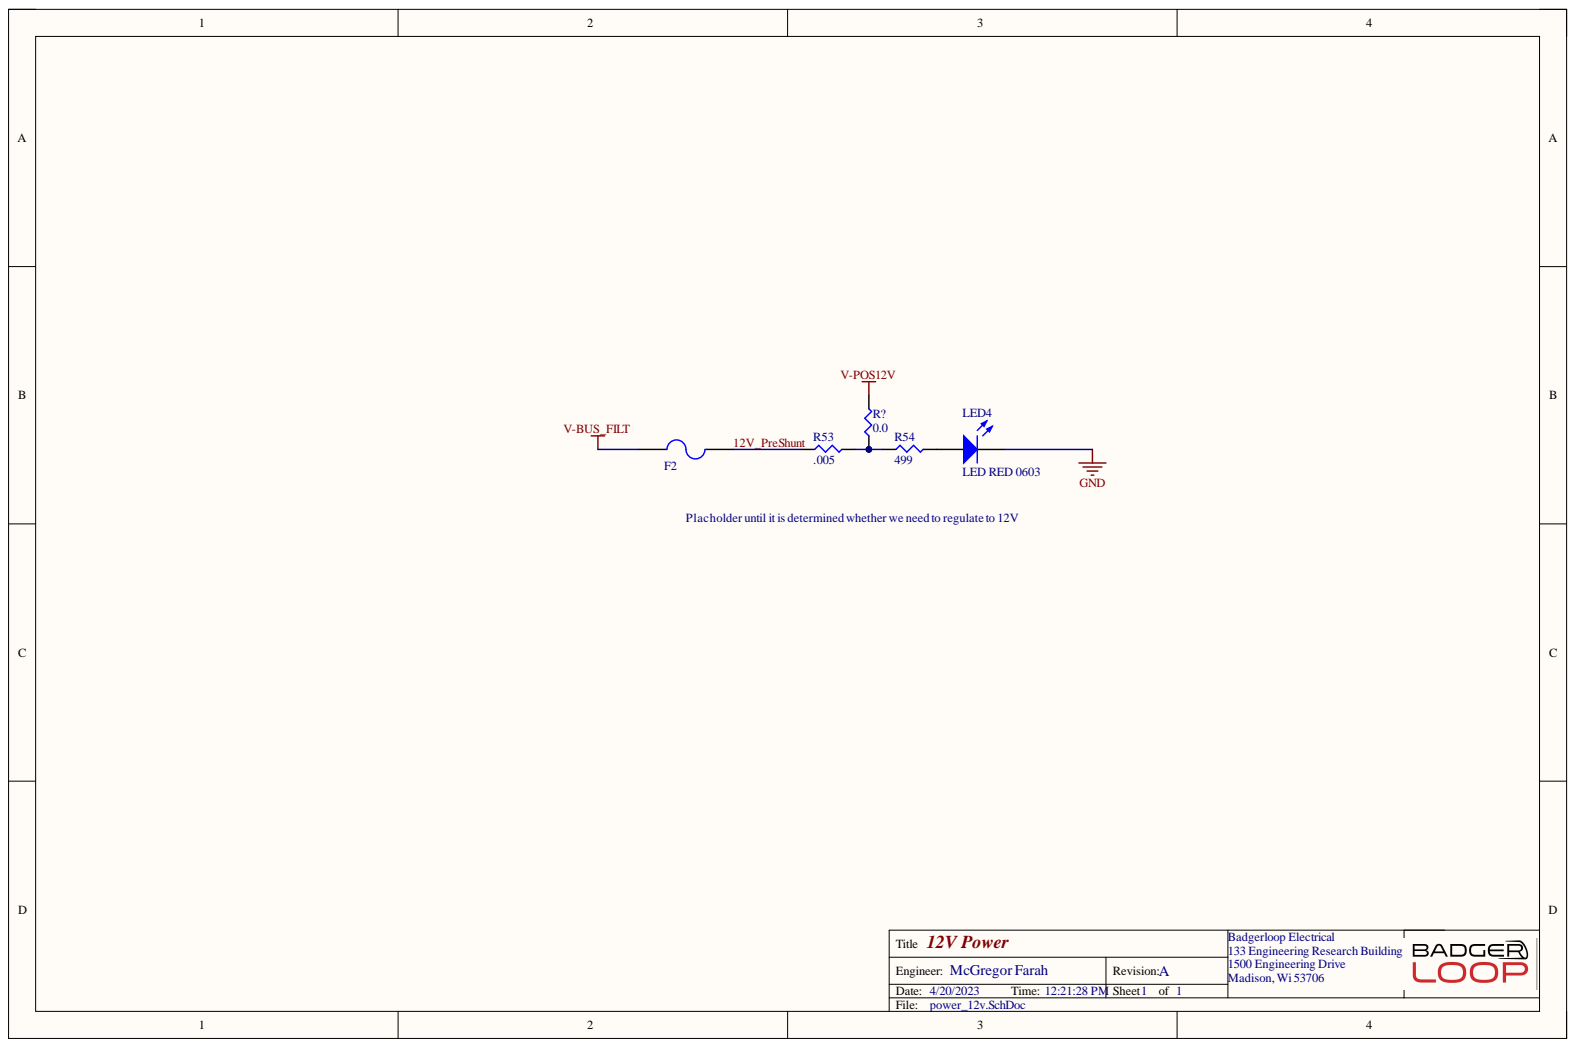
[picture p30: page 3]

Placholder until it is determined whether we need to regulate to 12V

12V Power Title | Badgerloop Electrical 133 Engineering Research Building 1500 Engineering Drive Madison,Wi 53706

McGregor Farah Engineer: | A Revision:

Date: 4/20/2023 Time: 12:21:28 PM | Sheet 1 of 1

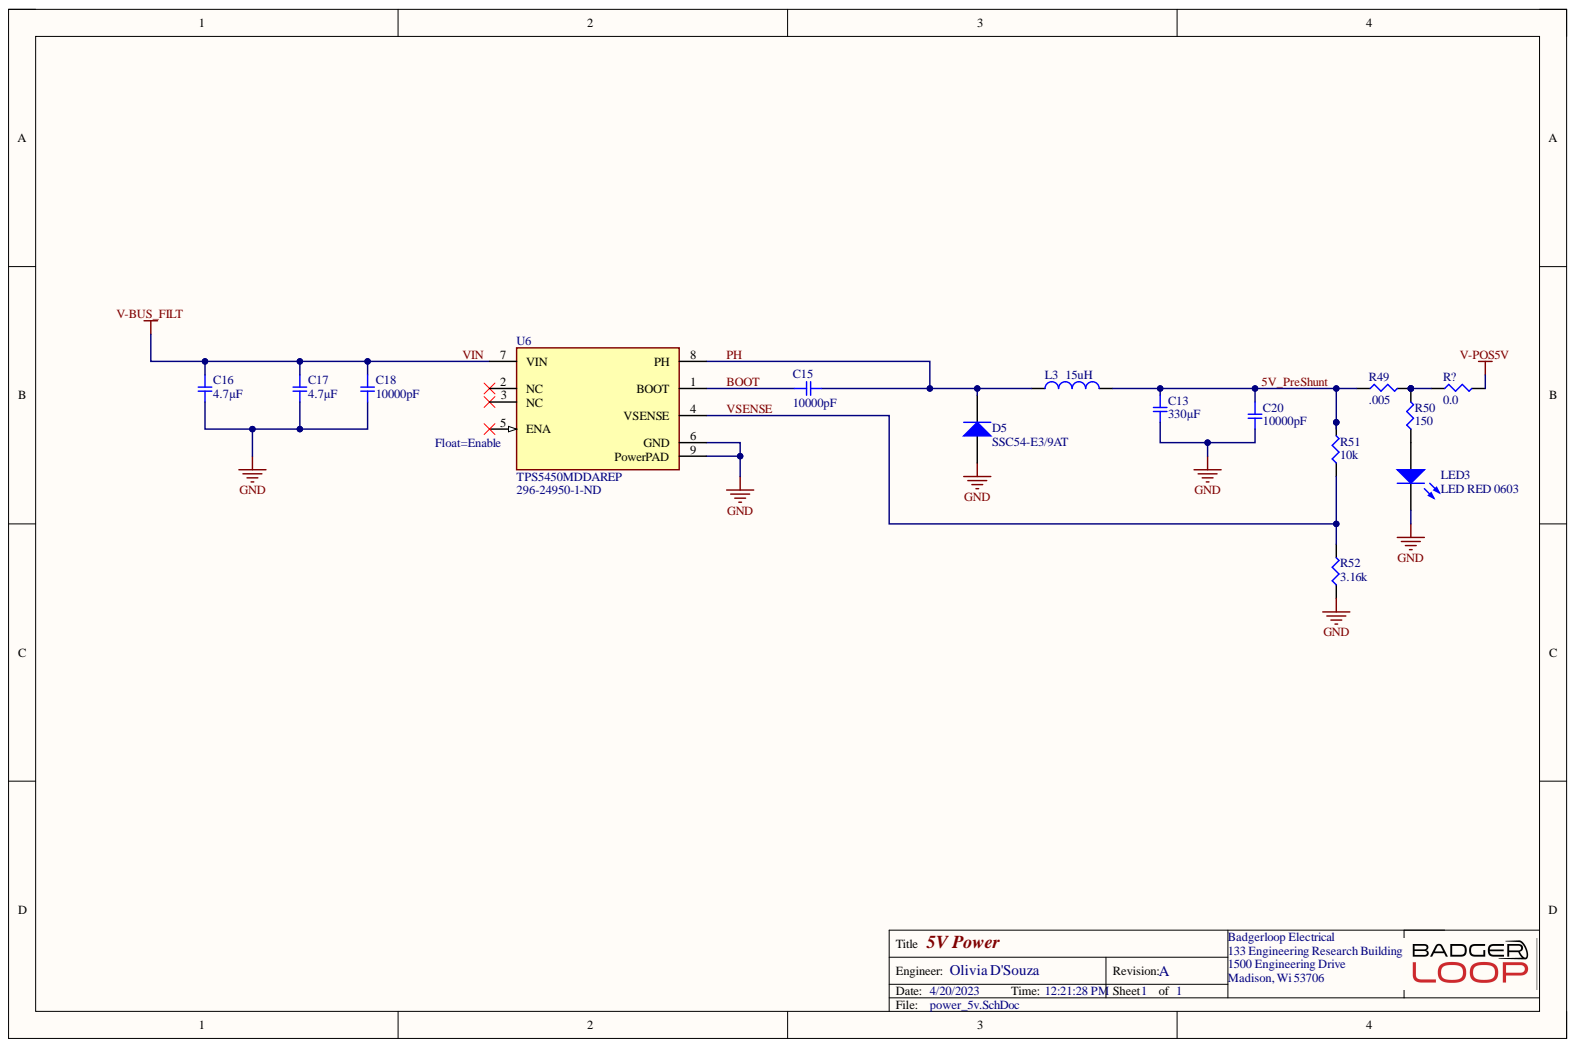
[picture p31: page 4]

5V Power Title | Badgerloop Electrical 133 Engineering Research Building 1500 Engineering Drive Madison,Wi 53706

Olivia D'Souza Engineer: | A Revision:

Date: 4/20/2023 Time: 12:21:28 PM | Sheet 1 of 1

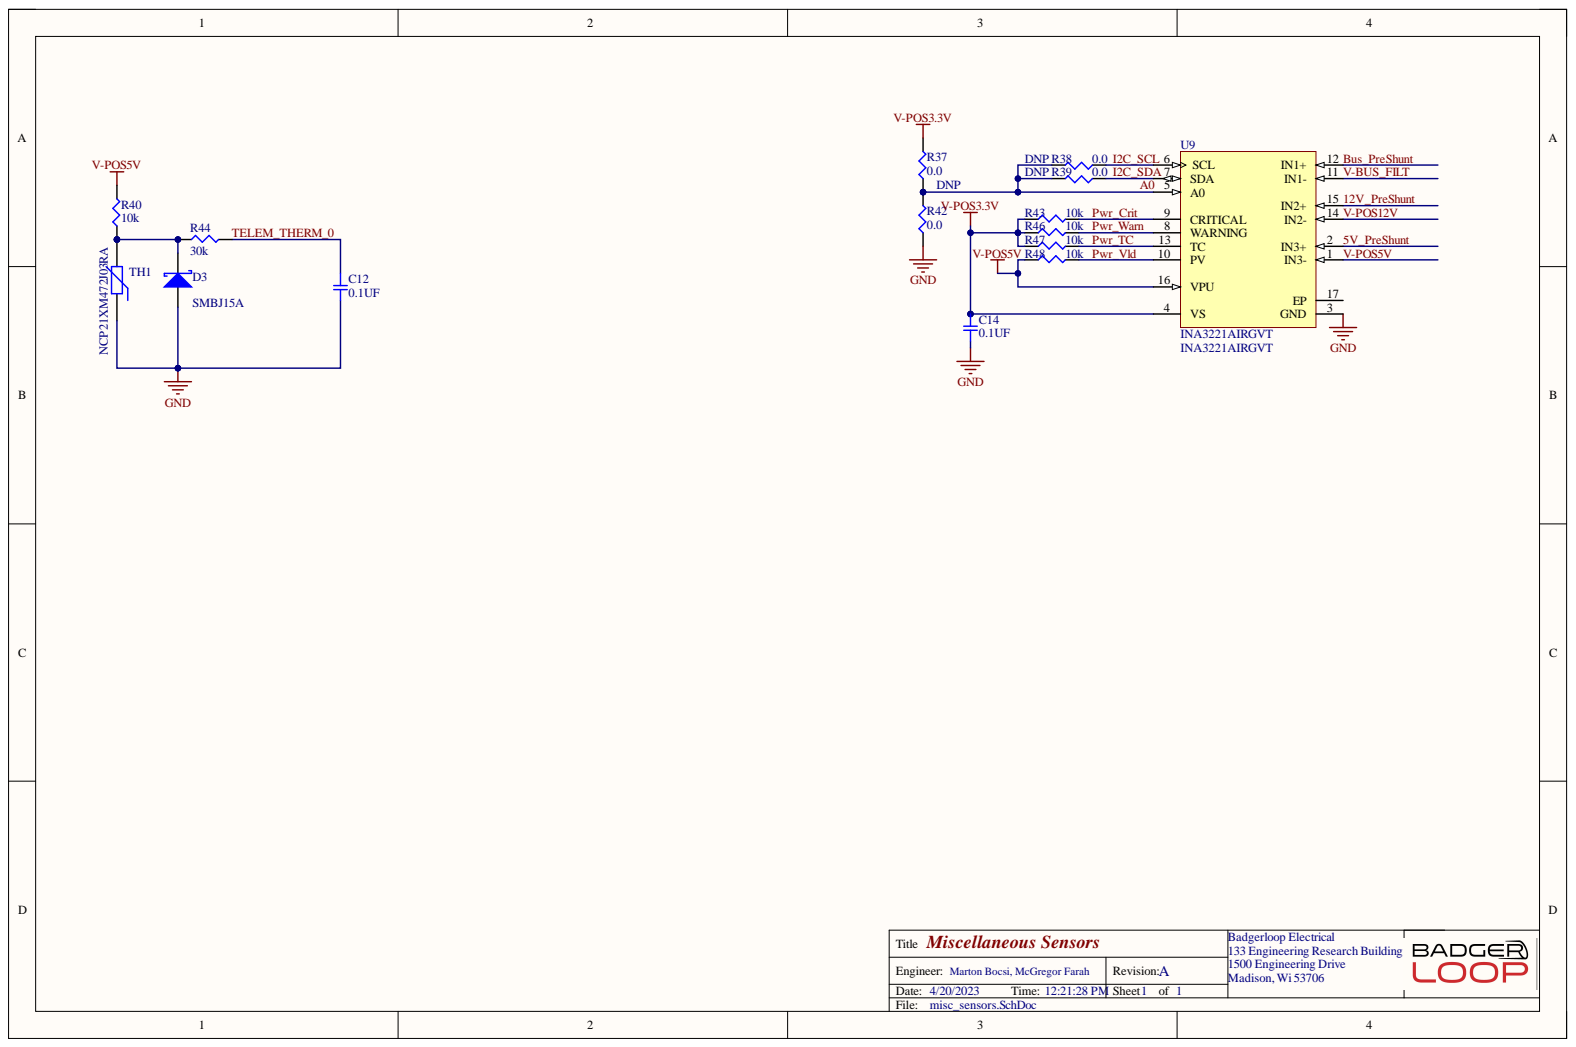
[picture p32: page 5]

WARNING 8 CRITICAL 9 TC 13 PV 10

R48 10k Pwr_Vld

VPU 16

Miscellaneous Sensors Title | Badgerloop Electrical 133 Engineering Research Building 1500 Engineering Drive Madison,Wi 53706

Marton Bocsi, McGregor Farah Engineer: | A Revision:

Date: 4/20/2023 Time: 12:21:28 PM | Sheet 1 of 1

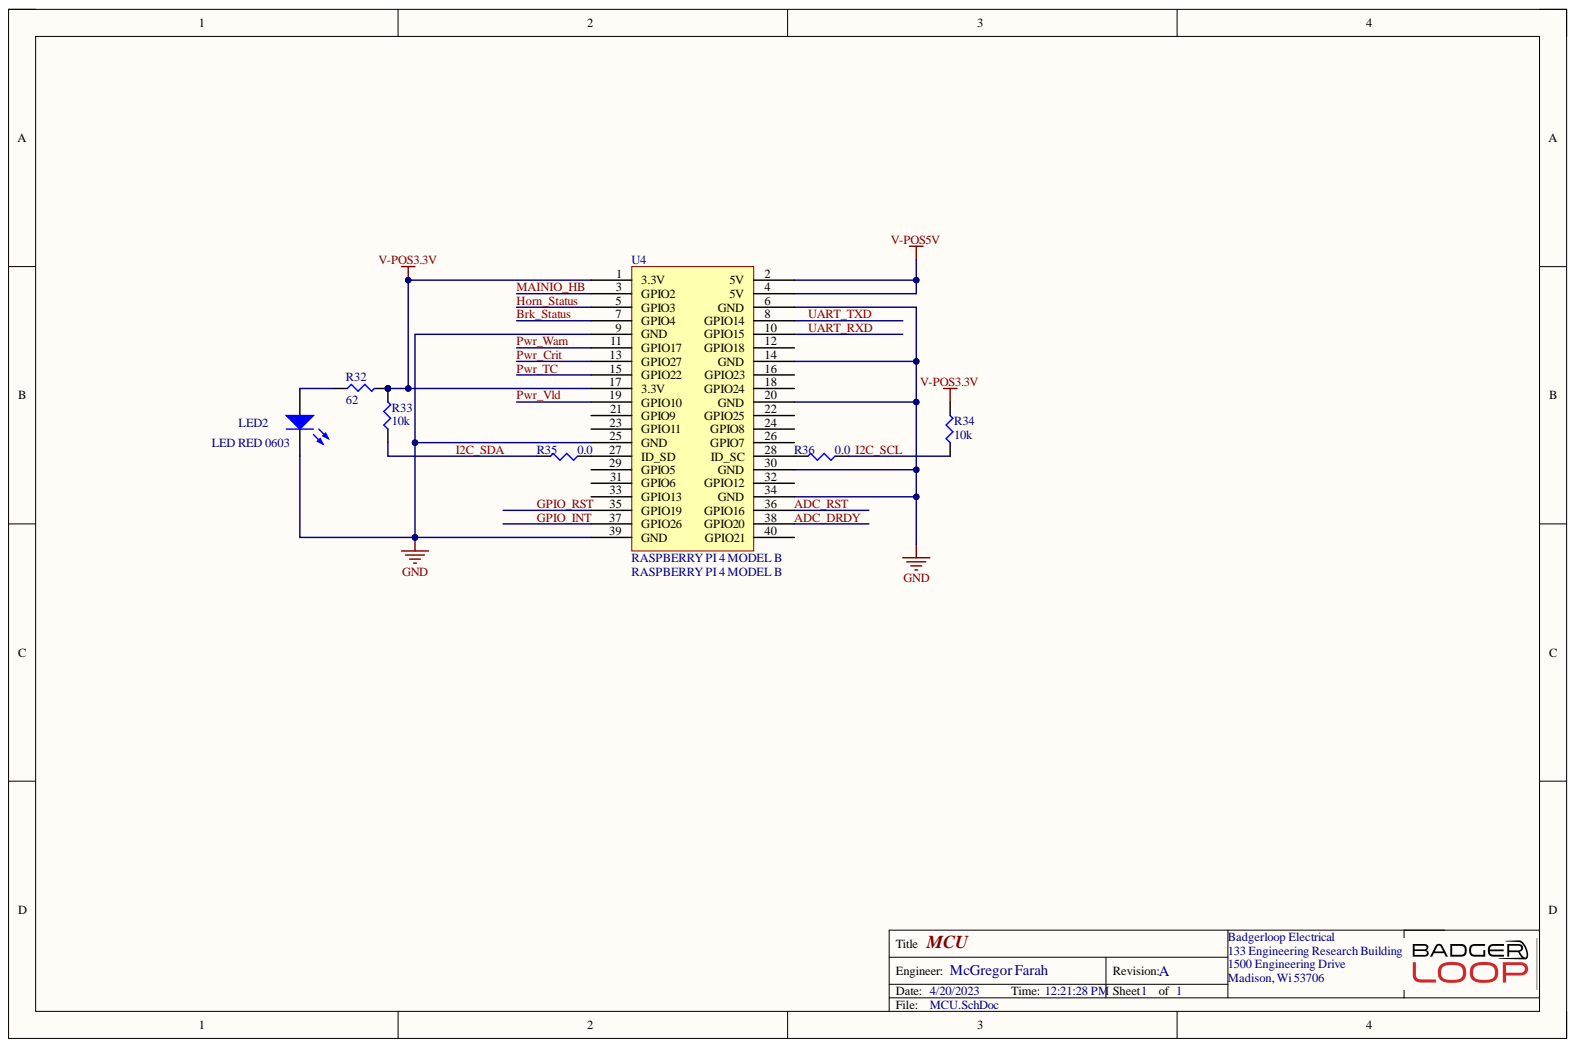
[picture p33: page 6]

MCU Title | Badgerloop Electrical 133 Engineering Research Building 1500 Engineering Drive Madison,Wi 53706

McGregor Farah Engineer: | A Revision:

Date: 4/20/2023 Time: 12:21:28 PM | Sheet 1 of 1

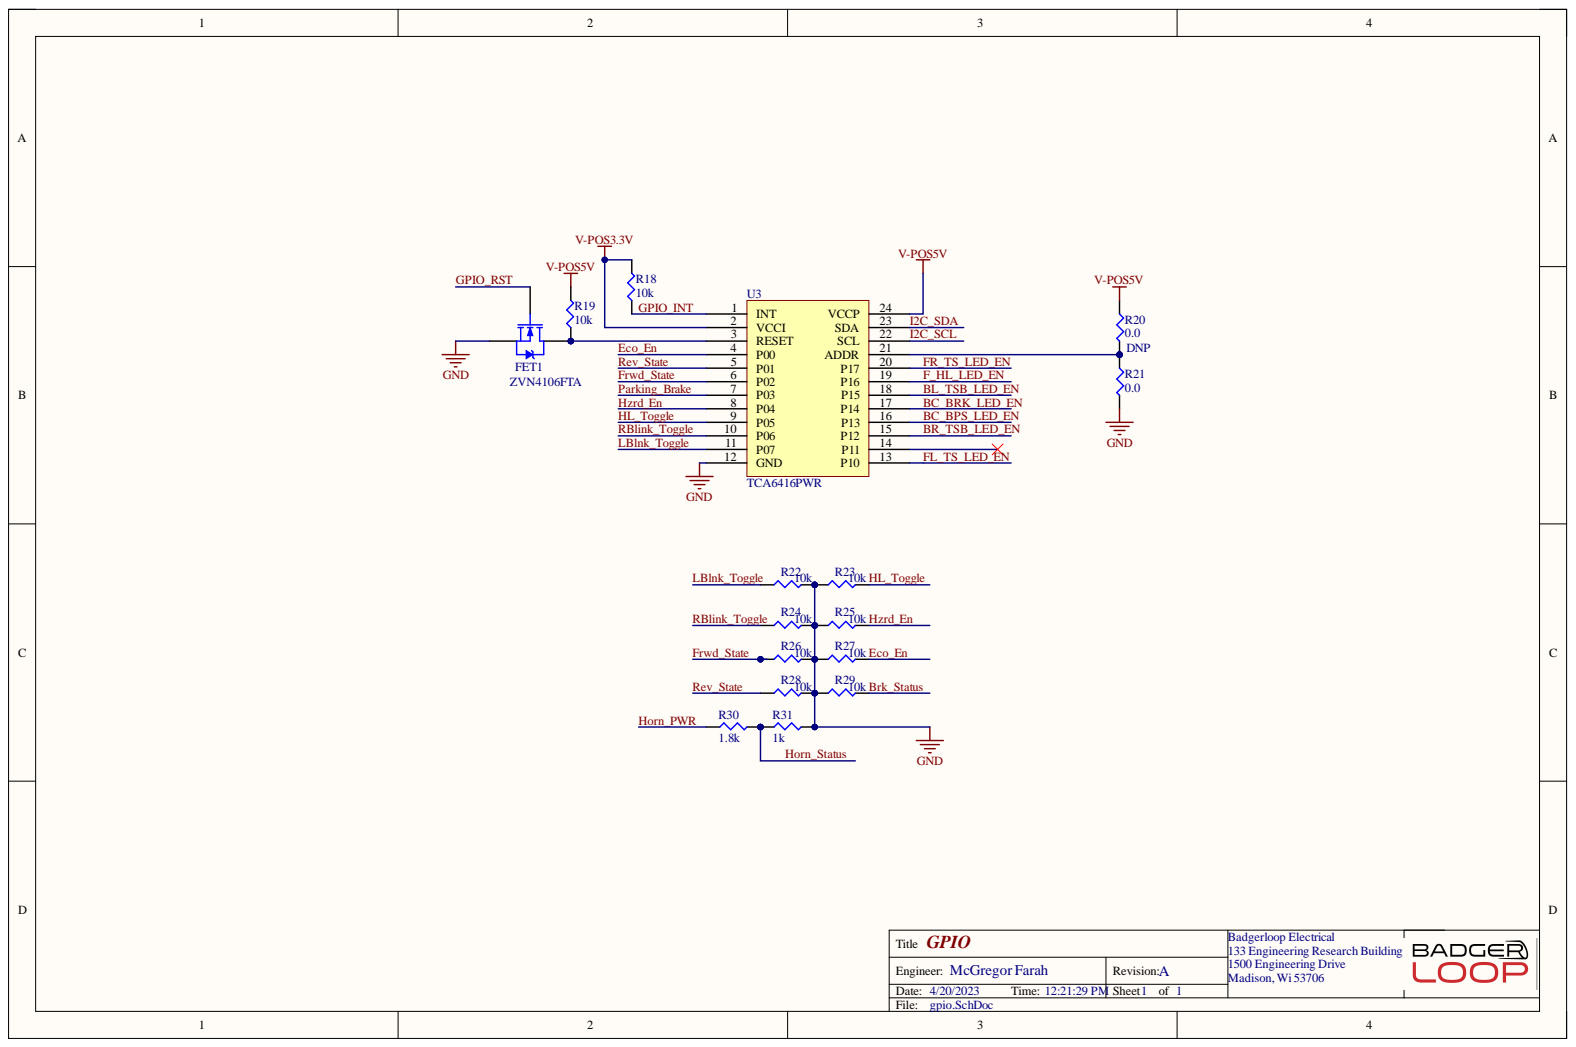
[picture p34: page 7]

GPIO Title | Badgerloop Electrical 133 Engineering Research Building 1500 Engineering Drive Madison,Wi 53706

McGregor Farah Engineer: | A Revision:

Date: 4/20/2023 Time: 12:21:29 PM | Sheet 1 of 1

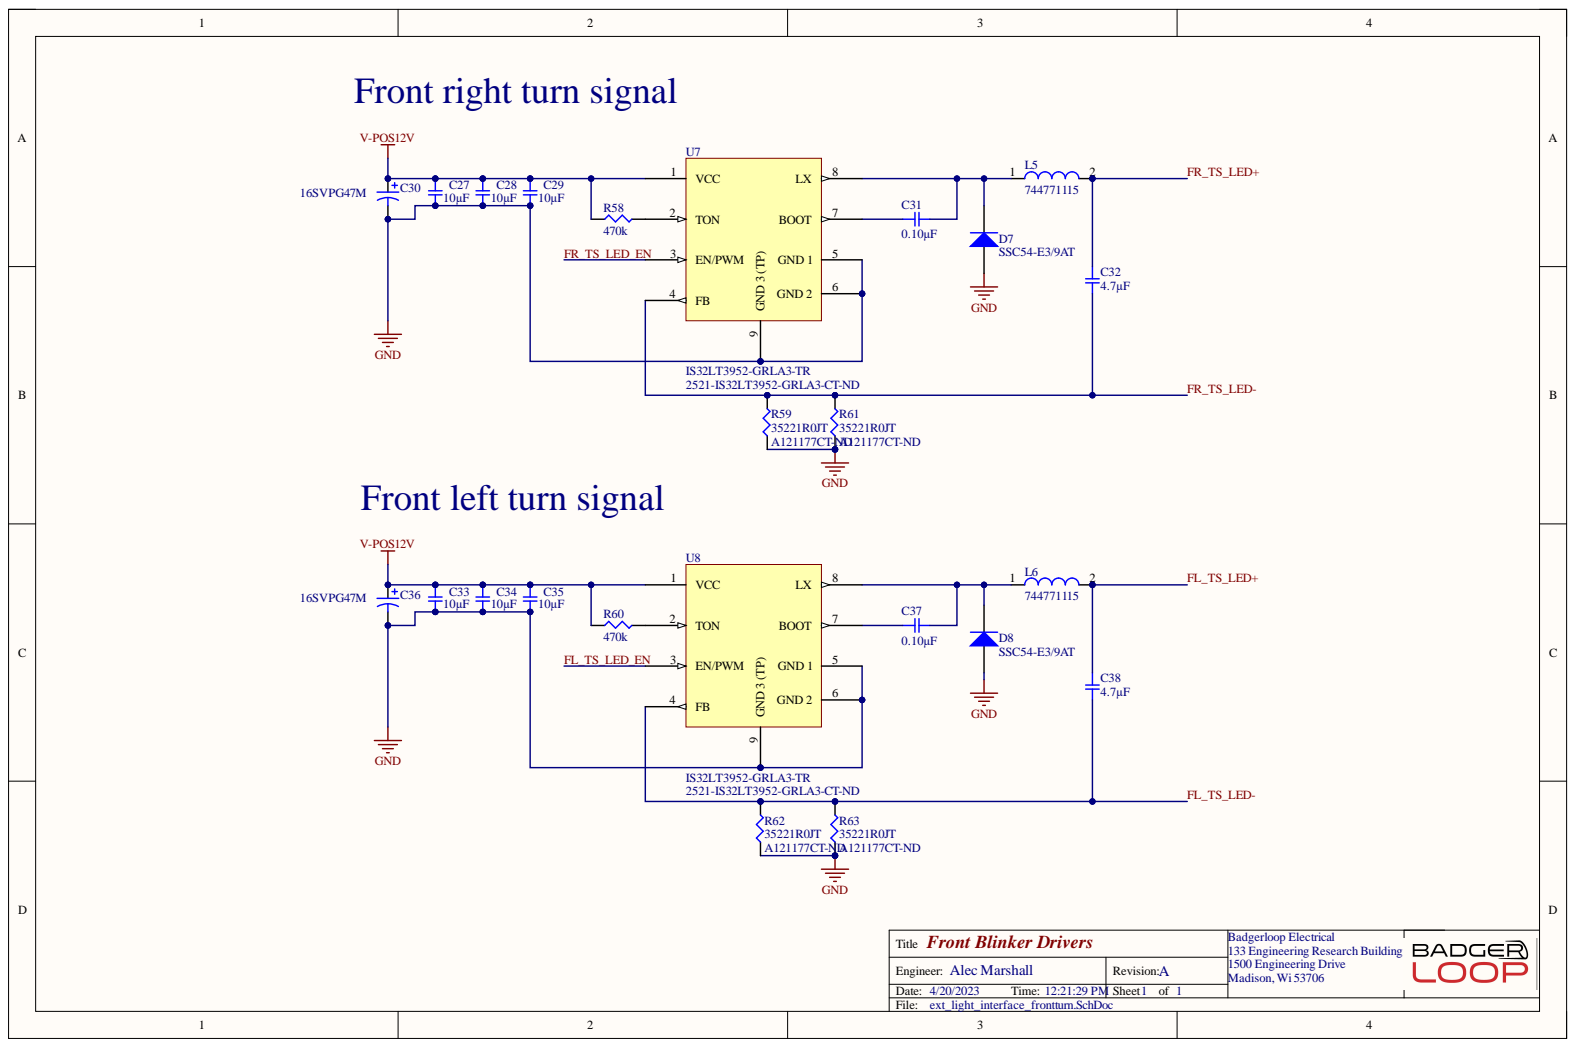
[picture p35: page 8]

Front right turn signal

Front left turn signal

Front Blinker Drivers Title | Badgerloop Electrical 133 Engineering Research Building 1500 Engineering Drive Madison,Wi 53706

Alec Marshall Engineer: | A Revision:

Date: 4/20/2023 Time: 12:21:29 PM | Sheet 1 of 1

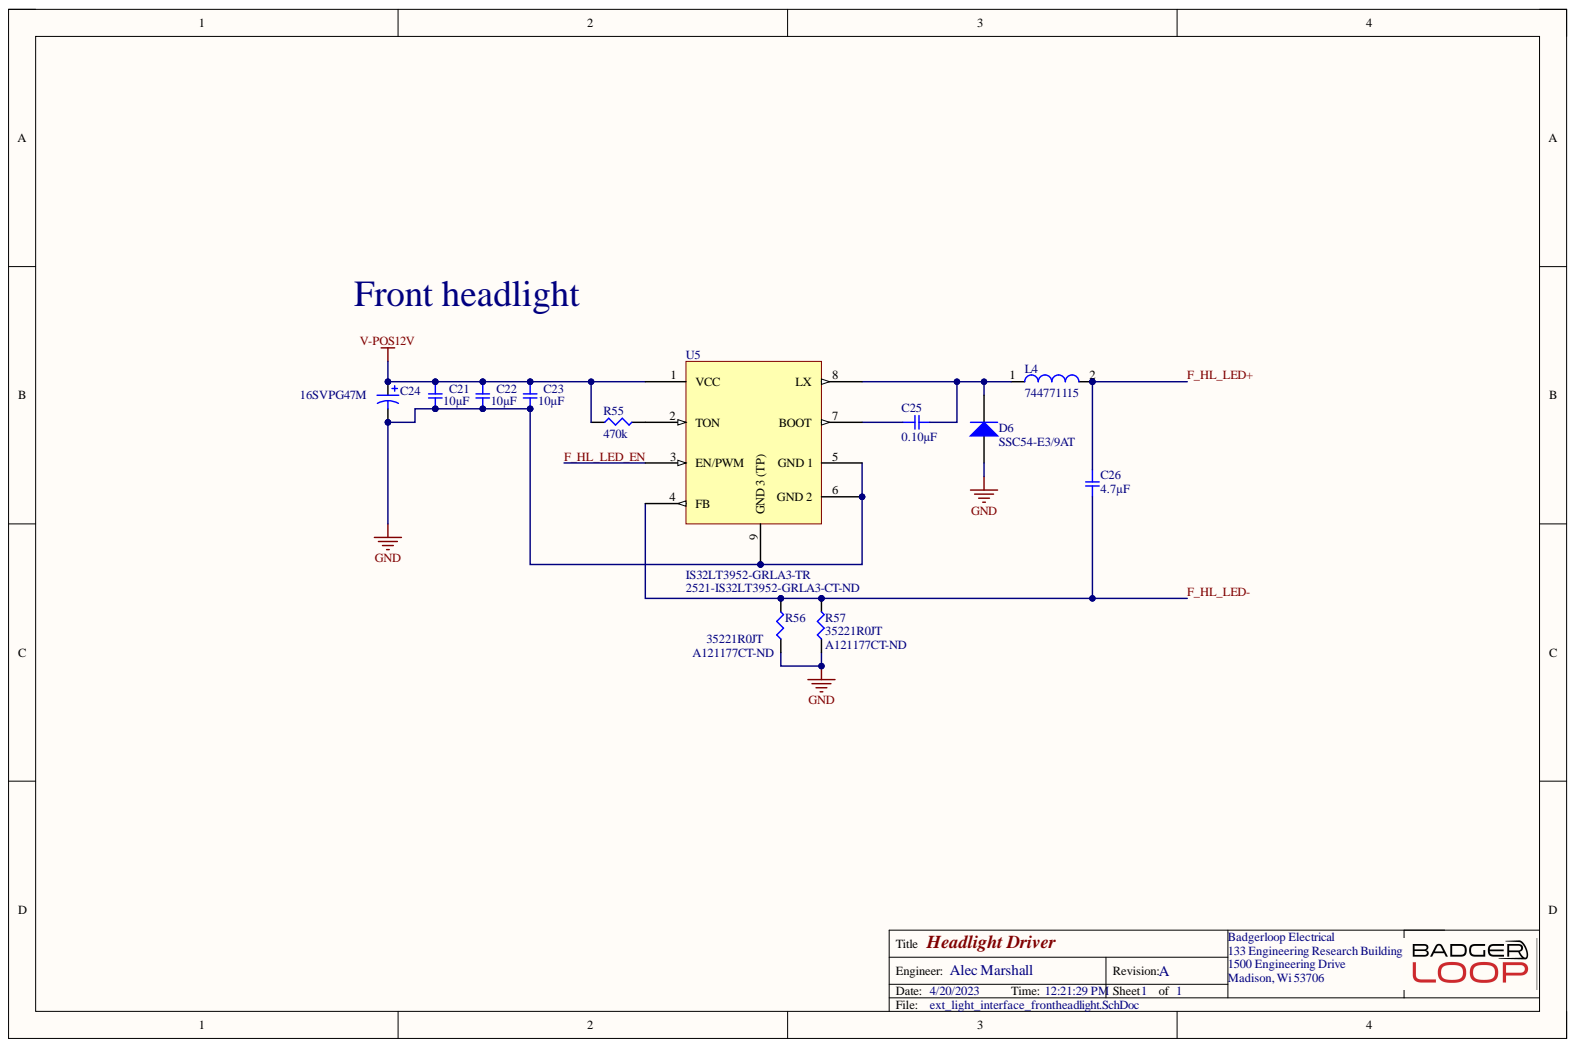
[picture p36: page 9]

Headlight Driver Title | Badgerloop Electrical 133 Engineering Research Building 1500 Engineering Drive Madison,Wi 53706

Alec Marshall Engineer: | A Revision:

Date: 4/20/2023 Time: 12:21:29 PM | Sheet 1 of 1

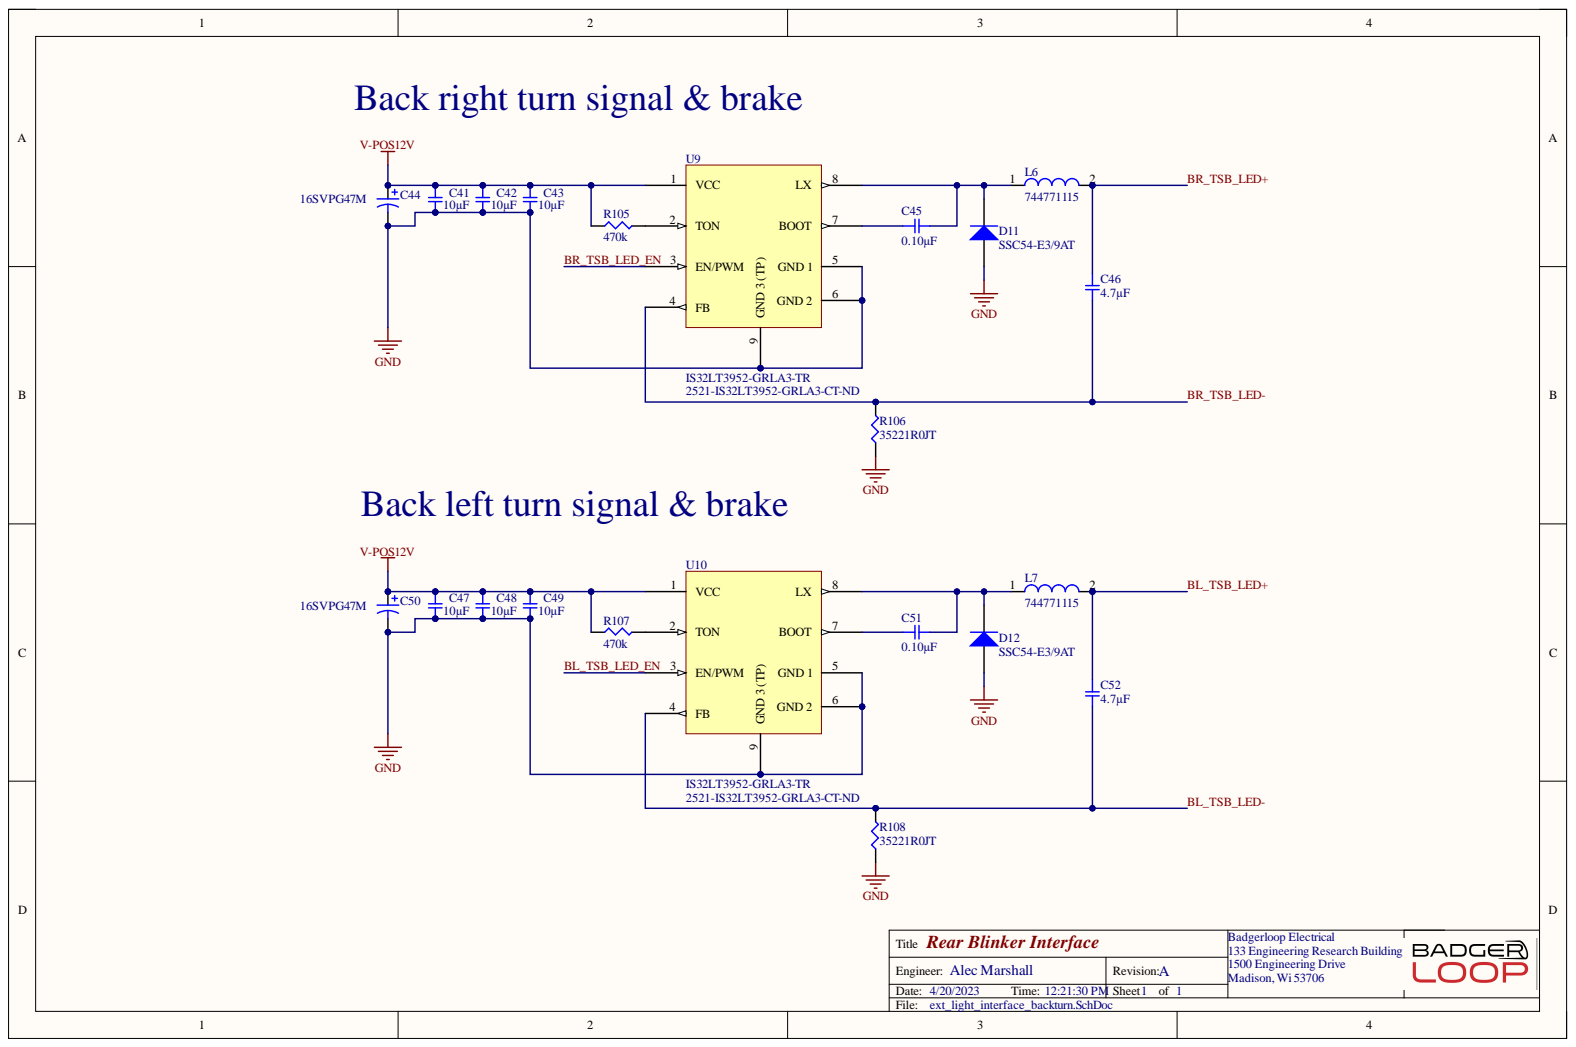
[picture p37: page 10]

Back right turn signal & brake

Rear Blinker Interface Title | Badgerloop Electrical 133 Engineering Research Building 1500 Engineering Drive Madison,Wi 53706

Alec Marshall Engineer: | A Revision:

Date: 4/20/2023 Time: 12:21:30 PM | Sheet 1 of 1

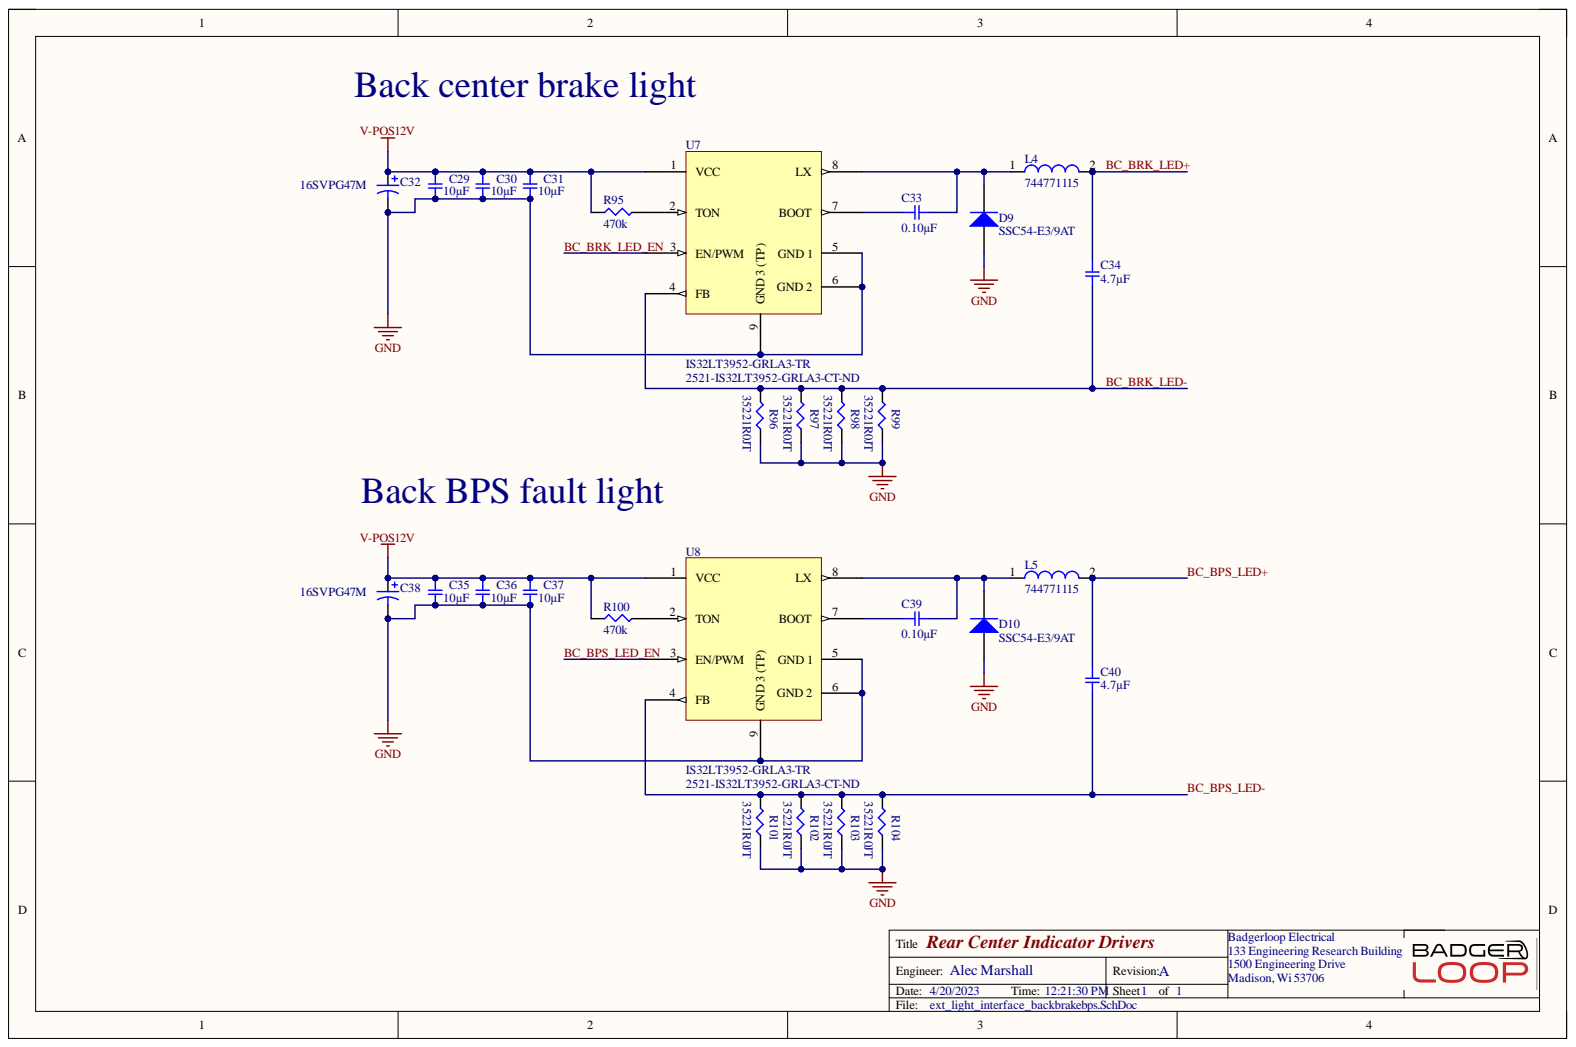
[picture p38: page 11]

Back center brake light

Back BPS fault light

Rear Center Indicator Drivers Title | Badgerloop Electrical 133 Engineering Research Building 1500 Engineering Drive Madison,Wi 53706

Alec Marshall Engineer: | A Revision:

Date: 4/20/2023 Time: 12:21:30 PM | Sheet 1 of 1

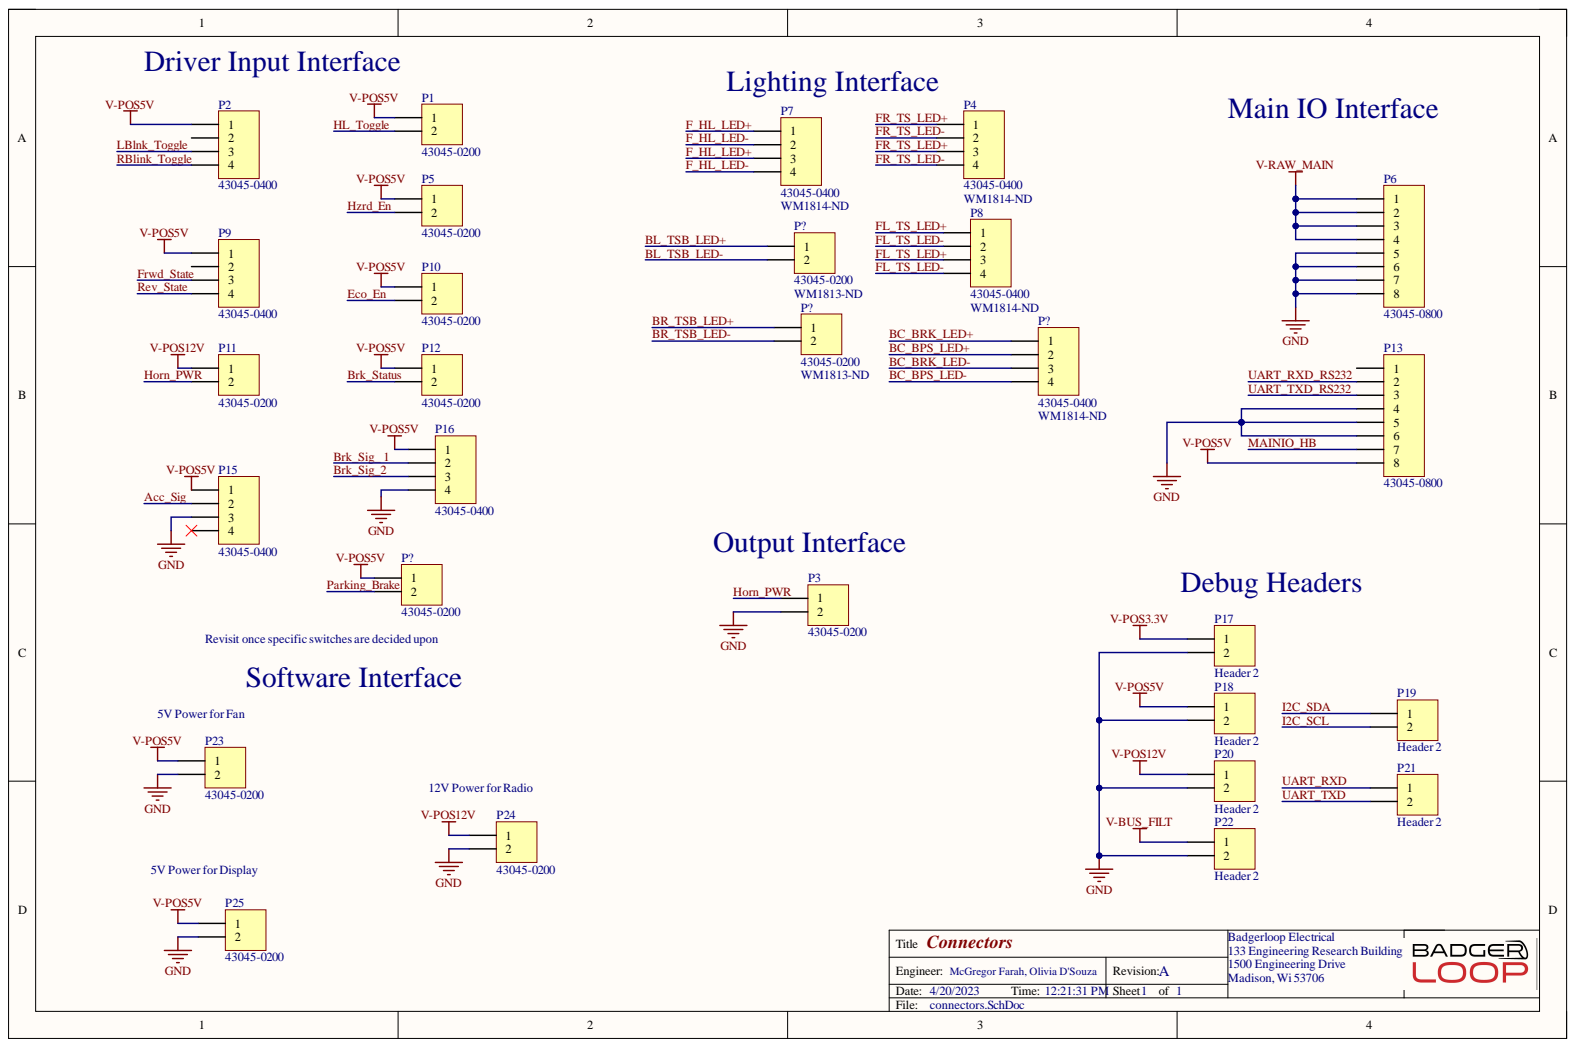
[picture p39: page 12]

Revisit once specific switches are decided upon
Software Interface


Bus Filter Title | Badgerloop Electrical 133 Engineering Research Building 1500 Engineering Drive Madison,Wi 53706

Marton Bocsi, McGregor Farah Engineer: | A Revision:

Date: 4/20/2023 Time: 12:21:31 PM | Sheet 1 of 1


R13 Brk_Sig_1 30k | AIN3 6 AIN2 7 | TELEM_THERM_0 R? Brk_Sig_2

AGND 5

ADC Title | Badgerloop Electrical 133 Engineering Research Building 1500 Engineering Drive Madison,Wi 53706

McGregor Farah Engineer: | A Revision:

Date: 4/20/2023 Time: 12:21:31 PM | Sheet 1 of 1


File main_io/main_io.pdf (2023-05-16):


Main IO Title | Badgerloop Electrical 133 Engineering Research Building 1500 Engineering Drive Madison,Wi 53706

Engineer: | Revision:
Date: 4/20/2023 Time: 12:20:58 PM | Sheet 1 of 2


Placholder until it is determined whether we need to regulate to 12V

12V Power Title | Badgerloop Electrical 133 Engineering Research Building 1500 Engineering Drive Madison,Wi 53706

McGregor Farah Engineer: | A Revision:

Date: 4/20/2023 Time: 12:20:56 PM | Sheet 1 of 1


5V Power Title | Badgerloop Electrical 133 Engineering Research Building 1500 Engineering Drive Madison,Wi 53706

McGregor Farah Engineer: | A Revision:

Date: 4/20/2023 Time: 12:20:57 PM | Sheet 1 of 1


Beaglebone Black Interface Title | Badgerloop Electrical 133 Engineering Research Building 1500 Engineering Drive Madison,Wi 53706

McGregor Farah Engineer: | A Revision:

Date: 4/20/2023 Time: 12:20:57 PM | Sheet 1 of 1



Motor Controller/BMS Interface Title | Badgerloop Electrical 133 Engineering Research Building 1500 Engineering Drive Madison,Wi 53706

M. Farah, A. Marshall, O. D'Souza Engineer: | A Revision:

Date: 4/20/2023 Time: 12:20:58 PM | Sheet 1 of 1


HV Controller Interface Title | Badgerloop Electrical 133 Engineering Research Building 1500 Engineering Drive Madison,Wi 53706

McGregor Farah Engineer: | A Revision:

Date: 4/20/2023 Time: 12:20:59 PM | Sheet 1 of 1


GPIO Title | Badgerloop Electrical 133 Engineering Research Building 1500 Engineering Drive Madison,Wi 53706

McGregor Farah Engineer: | A Revision:

Date: 4/20/2023 Time: 12:20:59 PM | Sheet 1 of 1


Connectors Title | Badgerloop Electrical 133 Engineering Research Building 1500 Engineering Drive Madison,Wi 53706

McGregor Farah Engineer: | A Revision:

Date: 4/20/2023 Time: 12:21:00 PM | Sheet 1 of 1


Bus Fi lter Titl e | B adge rloop Ele ctri c a l 133 Engine e ring R ese a r ch Buildi n g 1500 Engine e ring Dr iv e Madison, Wi 5370 6

Engine e r : Mar t o n B ocsi , McG reg o r Farah | A R evision :

Da te : 4/20/202 3 Time : 12:21:00 P M | She e t 1 o f 1


Clamping Diode Selection Reference :: https://e2e.ti.com/blogs_/b/industrial_strength/posts/how-to-choose-a-tvs-diode-for-rs-232-rs-485-and-can-based-on-voltage-ratings

Jump if board is terminating node

GND1 2

NC 5 | | CAN_L

* Title | Badgerloop Electrical 133 Engineering Research Building 1500 Engineering Drive Madison,Wi 53706

* Engineer: | * Revision:

Date: 4/20/2023 Time: 12:21:01 PM | Sheet 2 of 2


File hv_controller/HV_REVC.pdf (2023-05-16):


Digital Potentiometers and Nucleo

The Nucleo communicates with the BMS and uses the
potentioemeters to create a reference signal that allows
the MCand MPPT to charge to the correct levels.

CAN Baud rate max = 1Mbps
11th harmonic = 11Mbps
Speed oftransmission =C/2
11th harmonic λ = 33m
Wire lengths << 3m -> no controlled impedance needed

To route the tx and rx as
differential pairs. there is a naming
convention that need to be
followed. net pair must be named
with net label suffixes of _N and _P
CAN_TX : COMM_N
CAN_RX : COMM_P

GND1 2
RXD 3

GND1 7

Precharge Breakout Title | Badgerloop Electrical 133 Engineering Research Building 1500 Engineering Drive Madison,WI 53706

* Engineer: | 1 Revision:

Date: 4/1/2023 Time: 10:19:28 PM | Sheet 1 of 11


Verify All The Signals

Precharge Breakout Title | Badgerloop Electrical 133 Engineering Research Building 1500 Engineering Drive Madison,WI 53706

* Engineer: | * Revision:

Date: 4/1/2023 Time: 10:19:28 PM | Sheet 2 of 11


LED+ 1

1k | LED- 2

(-) LV_CMP_MC

(-) LV_CMP_MPPT


12V DC-DC Converter (Low Voltage Power)

1 2 | -Vout | HV_12V +Vin 1

-Vin 2 | 5 +Vout 7 NC 6



Add common
drain amplifier at
the output of the
latch??

Alatch circuit to keep MPS-CLOSE
high, unless reset by
LO_CONT_TELEM

Solar Array PCB (MPPT)

Precharge Breakout Title | Badgerloop Electrical 133 Engineering Research Building 1500 Engineering Drive Madison,WI 53706

* Engineer: | * Revision:

Date: 4/1/2023 Time: 10:19:30 PM | Sheet 6 of 11


Motor Controller Precharge Relays

* Engineer: | * Revision:

Date: 4/1/2023 Time: 10:19:31 PM | Sheet 7 of 11


MPPT Relays Title | Badgerloop Electrical 133 Engineering Research Building 1500 Engineering Drive Madison,Wi 53706

* Engineer: | * Revision:

Date: 4/1/2023 Time: 10:19:32 PM | Sheet 8 of 11


HV_OUT_MPPT
will be connected to
the MPPT

Main Power Switch Title | * *

* Engineer: | * Revision:

Date: 4/1/2023 Time: 10:19:32 PM | Sheet 9 of 11


If power path
controller on the board
does not work for
some reason we will
use this screw terminal
to connect the output
of the DCDC to input
of power path on
external board.

* Title | * *

* Engineer: | * Revision:

Date: 4/1/2023 Time: 10:19:33 PM | Sheet 10 of 11


P 4 3
123

Titl e | ****

Engine e r : | * R evision :

Da te : 4/1/202 3 Time : 10:19:34 P M | She e t 1 1 o f 1 1


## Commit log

2021-08-22 set up design workspace and add template project
    [Sheet1.SchDoc, board_template.PcbDoc, board_template.PrjPcb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]
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2021-10-28 Setup the HV schematics and filled in LV outlines
    [connectors.SchDoc, contactors.SchDoc, cover.SchDoc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]
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2021-11-02 Create separte relay schematics for each pre charge and add DCDC converter
    [hv_controller.PrjPcb, motor_controller_relays.SchDoc, mppt_relays.SchDoc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]
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2021-11-05 Add schematics for Main Power Switch (Contactors) and Precharge Circuits
    [contactors.SchDoc, motor_controller_relays.SchDoc, mppt_relays.SchDoc]
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2021-12-14 fixed capacitor orientation
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2021-12-14 add files to project and initial schematic work, modify sim for synch boost
    [Connectors.SchDoc, Converter_calculations.xlsx, Nucleo.SchDoc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]
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2021-12-14 work on POL converters and add same 0.1uf to all sheets
    [Connectors.SchDoc, Nucleo.SchDoc, POL_converter.SchDoc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]
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2021-12-15 add correct capacitor and finish LDO
    [Connectors.SchDoc, Nucleo.SchDoc, POL_converter.SchDoc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]
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2021-12-16 restructure telemetry situation, add analog mux for viewing thermal telemetry
    [Nucleo.SchDoc, boost_converter.SchDoc, boost_converter_telem.SchDoc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]
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2021-12-17 fix pin type on tmux
2021-12-17 clear all errors
    [global_telem.SchDoc]
2021-12-18 get annotation on board level correct, import into layout
    [Connectors.SchDoc, Nucleo.SchDoc, POL_converter.SchDoc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]
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2021-12-28 add diode component and fix others
2021-12-28 replace diodes with schottky and initial placement on all components
    [POL_converter.SchDoc, global_telem.SchDoc, mppt.PrjPcb]
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2021-12-31 more work on routing, just LV CAN left
    [POL_converter.SchDoc, mppt.PrjPcb]
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2022-01-12 fix routing issue on side of board
    [mppt.GBL, mppt.GBO, mppt.GBP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]
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2022-01-14 add pwm note, work on writeup, and add step file
    [boost_converter.SchDoc]
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2022-01-14 fix a couple more typos
2022-01-17 add RC filter to string in telem, regenerate outputs
    [Bill of Materials-mppt.xlsx, POL_converter.SchDoc, boost_converter_telem.SchDoc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]
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2022-01-18 fix two more 0.1uf resistors to correct part
    [Bill of Materials-mppt.xlsx, POL_converter.SchDoc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]
2022-01-19 update board to fix free dfm errors
    [mppt.GBL, mppt.GBO, mppt.GBP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]
2022-01-23 add boms to output for ordering, including one from digikey
    [Bill of Materials-mppt.xlsx, mppt.PrjPcb]
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2022-01-29 This commit acts as a merge of the HV and lV branches
    Opted to just copy in the most updated versions of each SchDoc to avoid
    any problems.
    The commit histories for each branch will just be located in
    the respective remote branches if anything needs to be referenced. Based
    on our workflow this didn't seem important to carry forward hence why I
    opted to just copy in the correct files.
    [MCU.SchDoc, RTC.SchDoc, Serial_Interface.SchDoc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]
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2022-02-02 Tweaked some Main IO Schematics due to stock constraints
    [RTC.SchDoc, Serial_Interface.SchDoc, beaglebone.SchDoc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]
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2022-02-06 swap oos components for the in stock ones
    [RTC.SchDoc, Serial_Interface.SchDoc, adc.SchDoc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]
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2022-02-14 Added component annotations (and also a few other things)
    [MCU.SchDoc, RTC.SchDoc, Serial_Interface.SchDoc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]
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2022-03-11 add anderson connector and fix pinout on NPN
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2022-03-14 replace 12V circuit and nucleo, resize board
    [Nucleo.SchDoc, POL_converter.SchDoc]
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2022-03-20 driver IO push, but its not broken this time
    [MCU.SchDoc, driver_io.PrjPcb]
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2022-03-30 final driver io rev a changes before order attempt, main io revisions from Shelby's review, and updated nets on schematics
    [misc_sensors.SchDoc, power_5V.SchDoc, power_5v.SchDoc]
2022-03-31 Driver IO PCB and Main IO PCB Rev A ordered--Driver IO approved by AC and Main IO on hold, some clearances need to be higher. Going on my PC to do that now w this push:)
    [Serial_Interface.SchDoc, connectors.SchDoc]
2022-03-31 final LV Rev A edits. These boards are ordered, approved by AC. Also added the Main IO Gerbers
    [main_io.GBL, main_io.GBO, main_io.GBP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]
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2022-04-01 add correct drive resistors
    [boost_converter.SchDoc, mppt.PrjPcb, pwm_conditioning.SchDoc]
2022-04-02 final changes to Rev A main io & driver IO pcb's: AC approved. Modified component footprints to comply with AC rules.
    [driver_io.GBL, driver_io.GBO, driver_io.GBP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]
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2022-04-14 get rid of unity gain buffers and change output divider
    [boost_converter_telem.SchDoc, global_telem.SchDoc]
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2022-04-16 add discharge circuit and ov protection resistor to schematics
    [Nucleo.SchDoc, boost_converter.SchDoc, global_telem.SchDoc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]
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2022-04-20 add firmaware change notes and add pulldown on mcu_boost_enable signal
    [Nucleo.SchDoc, boost_converter.SchDoc, boost_converter_telem.SchDoc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]
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2022-08-29 fixed fet footprint ppc
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2022-09-01 fixing pcb
2022-09-01 fixing pcb again
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2022-09-05 fixed schematic for capacitor
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2022-09-06 shortening traces
2022-09-06 fixing traces again
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2022-09-07 fixed resistor connection
2022-09-07 fixed resistors
    [mppt_relays.SchDoc]
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2022-09-07 fixing ppc trace issues
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2022-09-08 replaced relays
    [mppt_relays.SchDoc]
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2022-09-11 traces fixing
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2022-10-04 still trying to fix the sensor
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2022-10-05 reverting to previous commit to fix pcb prj
    [MCU.SchDoc, gpio.SchDoc]
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2022-10-05 fixing lighting/current monitor ic
    [ext_light_interface_frontheadlight.SchDoc, ext_light_interface_frontturn.SchDoc, misc_sensors.SchDoc]
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2022-10-05 fixed design rules
    [driver_io.PrjPcb]
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2022-10-05 gerbers after fixing hold issues
    [main_io.GBL, main_io.GBO, main_io.GBP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]
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2023-04-19 MCC rev b final changes, ready for review
    [Connectors.SchDoc, Nucleo.SchDoc, mcc.PcbDoc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]
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2023-04-19 added headers, fixed analog pinout
    [Nucleo.SchDoc, mcc.PcbDoc]
2023-04-20 added nucleo to mcu doc and removed rtc
    [RTC.SchDoc, beaglebone.SchDoc]
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2023-04-20 main io and driver io schematic changes prior to review
    [MCU.SchDoc, adc.SchDoc, connectors.SchDoc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]
2023-05-16 MCC rev B fixes (MCC rev B.5), updated schematic headers
    [CAN.SchDoc, Connectors.SchDoc, Nucleo.SchDoc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]
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2023-05-16 changed digital pot and a couple other small changes
    [connectors.SchDoc, ic_madness.SchDoc, mc_signals.SchDoc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]
2023-05-16 Fixed footprints and started layout
    [connectors.SchDoc, ic_madness.SchDoc, mc_signals.SchDoc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]
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2023-05-16 hv lv fix
    [connectors.SchDoc, ic_madness.SchDoc, volt_sensor_breakout.PcbDoc]
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2023-05-16 added risk reduction design. also I'm committing the final rev of the battery board on this branch hehehe
    [battery_bank-003.GBL, battery_bank-003.GBO, battery_bank-003.GBP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]
2023-05-16 alpha layout complete. alpha routing to be done next
    [connectors.SchDoc, ic_madness.SchDoc, mc_signals.SchDoc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]
2023-05-16 layout and schematic changes up until reformatting voltage sense & adding in second latch circuit
    [connectors.SchDoc, ic_madness.SchDoc, mc_signals.SchDoc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]
2023-05-16 changed the name of the schematics to accurately reflect the rooms on the layout: voltage sense & latch are on their own pages now, with MC on the top & MPPT on the bottom
    [latch.SchDoc, mc_signals.SchDoc, mppt_signals.SchDoc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]
2023-05-16 added a couple pages for better room organzation. commiting so I can change the name of a schematic
    [12V dc-dc converter.SchDoc, connectors.SchDoc, inverter.SchDoc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]
2023-05-16 Saturday afternoon update from me. Mdrihul is taking over to import some of the extra stuff & then I'll go back and finish routing the OG stuff.
    [digital.SchDoc]
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2023-05-16 voltage sense breakout layout. See HV channel for full decription / status
    [12V dc-dc converter.SchDoc, connectors.SchDoc, digital.SchDoc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]
2023-05-16 final voltage sense breakout changes, including manufacturing files and design guides
    [12V dc-dc converter.SchDoc, connectors.SchDoc, digital.SchDoc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]
2023-05-16 All hv schematic added, schematics still out to date
    [dc_dc_converter.SchDoc, main_power_switch.SchDoc, motor_controller_relays.SchDoc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]
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2023-05-16 Powerpath layout and schematic changes need to be done
    [12V dc-dc converter.SchDoc, connectors.SchDoc, digital.SchDoc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]
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2023-05-16 All updated schematics and layout arranged, a bit more work need to go on voltage sense and latch room
    [connectors.SchDoc, powerpath_controller.SchDoc, voltage_sense.SchDoc]
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2023-05-16 fixed all the connectors, horizontal on driver and vertical on main
    [connectors.SchDoc]
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2023-05-16 fixed lv -> hv connector to match hv
    [connectors.SchDoc]
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
